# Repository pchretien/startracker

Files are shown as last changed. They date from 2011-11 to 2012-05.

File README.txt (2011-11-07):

Description

This is a merge of the two previous Stars Trackers I made. I wanted a model that could be both manual and motorized. This thing is "really" a work in progress since I have not taken any picture with it yet. In the next few days the moon will rise late so I'll give it a shot at the first clear sky.

This type of astrophotography mount is often called a barndoor mount, a scotch mount or a Haig mount. This mount allows you to take long exposure of the night sky by canceling out the apparent motion of the stars in the sky. 

You can get more information on this type of device on Wikipedia:
en.wikipedia.org/wiki/Barn_door_tracker.

The NEMA17 motor is driven by an Arduino arduino.cc and the Adafruit Motorshield adafruit.com. I am still working on the Arduino software. The objective is to compensate for the error induced by the linear motion trying to emulate a constant speed rotation.

I made a short video to demonstrate hot to change from the motorized version to the manual version of the Stars Tracker. 
youtube.com/watch?v=pLnhl2p-kOQ&feature=feedu

The drawings have been made using Sketchup. The original drawings can be found in the starstrackerv2.0.zip file.
Instructions

Print and assemble ... the important dimension is the distance between the center of the hinge and the pivots, which is 145mm.

The non-printed parts you will need:

Main assembly:
--------------
2x 3/8" threaded rod 6.25" long
8x 3/8" nuts
1x 3/8" bolt 3/4" long (camera head)
4x 608 bearings
1x M6x35 8mm shoulder bolt
3x M8 washers
1x M6 nut
1x 1/4" nut (tripod attachment)
1x 10mm diameter tube for polar alignment

Motor assembly:
---------------
4x M3x12 bolts
2x M3x8 bolts (coupling)
2x M3 nuts (coupling)
1x NEMA17 stepper motor
1x 1/4" 20TPI threaded rod 6" long
1x 10mm diameter and 20mm long cross-dowel with a threaded hole

Manual assembly:
----------------
5x 1/4" nuts
1x 1/4" butterfly nut
2x 3/16" #12 washers
1x 1/4" 20TPI threaded rod 6" long
1x 10mm diameter and 20mm long cross-dowel with a threaded hole

Electronic:
-----------
1x Arduino arduino.cc
1x Adafruit Motorshield adafruit.com/products/81

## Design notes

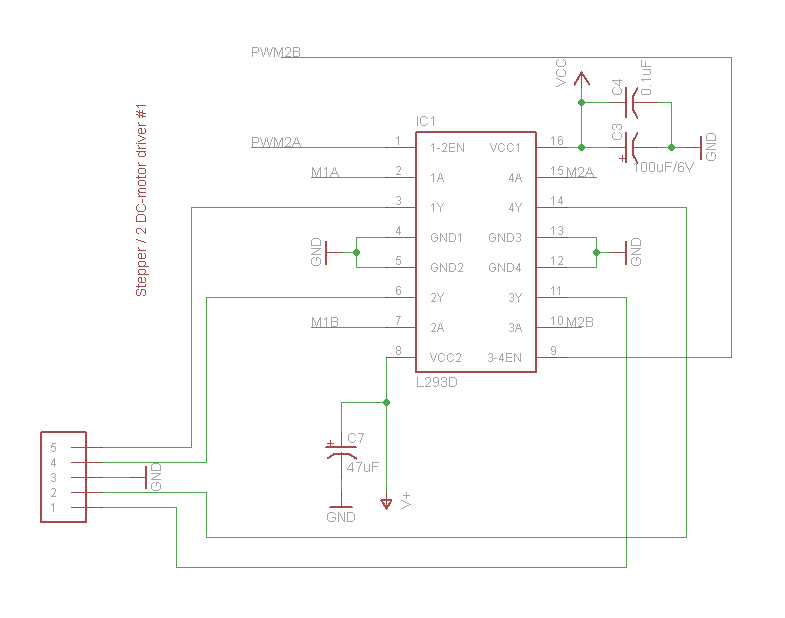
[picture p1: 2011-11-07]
L293Stepper.png

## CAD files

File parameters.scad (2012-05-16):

//
// Star tracker parameters
// Philippe Chrétien (2012)
// philippe.chretien.gmail.com
//

// Threaded rod
t_rod_out_radius = 4.8; //mm

// Skate bearing 608
bearing_out_radius = 11.25; //mm
bearing_thickness = 7.75; //mm

// M3 bolts
m3_out_radius = 1.5; //mm

// M3 nut
nut_m3_radius = 3.5; //mm
nut_m3_thickness = 2.5; //mm

// 1/4 nut
nut_1_4_radius = 6.5; //mm
nut_1_4_thickness = 5.5; //mm

// 3/8 nut
bolt_3_8_head_radius = 8.5; //mm
bolt_3_8_head_thickness = 6.0; //mm

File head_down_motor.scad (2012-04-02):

include <parameters.scad>

hdm_base_x = 43.0;
hdm_base_y = 53.0;
hdm_base_z = 15.4;
hdm_curve_radius = 40;

hdm_base_in_x = 30;
hdm_base_in_y = 33;

hdm_side_holes_y = 7.7;
hdm_side_holes_radius = 4.1;

hdm_buffer = 0.01;

module head_down_motor()
{
difference()
{
	// Piece stock
	union()
	{
		intersection()
		{
			translate([-1*(hdm_base_x/2),0,0])
				cube([hdm_base_x,hdm_base_y,hdm_base_z]);

			translate([0,hdm_base_y-hdm_curve_radius,0])
				cylinder(r=hdm_curve_radius, h=hdm_base_z, $fn=18);
		}			

		translate([-1*(hdm_base_x/2),0,0])
			cube([hdm_base_x,top_width,top_height]);		
	}	

	translate([-1*(hdm_base_in_x/2),0,0])
		cube([hdm_base_in_x,hdm_base_in_y,hdm_base_z]);

	translate([0,hdm_base_y, hdm_base_z/2])
		rotate(a=90, v=[1,0,0])
			cylinder(r=t_rod_out_radius, h=hdm_base_y-hdm_buffer);

	translate([-1*(hdm_base_x/2)-hdm_buffer,hdm_side_holes_y, hdm_base_z/2])
		rotate(a=90, v=[0,1,0])
			cylinder(r=t_rod_out_radius, h=hdm_base_x+2*hdm_buffer);
}
}

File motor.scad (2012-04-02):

include <parameters.scad>

base_x = 42.0;
base_y = 25.0;
base_z = 5.5;
curve_radius = 30;

top_width = 6.25;
top_height = 20;

screw_x = 15.5;		// Relative to the motor head hole center
screw_z = 15.5;		// Relative to the motor head hole center
screw_radius = 1.75;
screw_head_radius = 3.25;
screw_head_depth = 2.5;

pin_y = 3;
pin_height = 3;
pin_radius = 4.5; // Increased size but not yet printed

motor_head_z = 26.5;
motor_head_radius = 11.5;

buffer = 0.01;

module motor_half_mount()
{
	difference()
	{
		// Piece stock
		union()
		{
			intersection()
			{
				translate([-1*(base_x/2),0,0])
					cube([base_x,base_y,base_z]);

				translate([0,base_y-curve_radius,0])
					cylinder(r=curve_radius, h=base_z);
			}			

			translate([-1*(base_x/2),0,0])
				cube([base_x,top_width,top_height]);

			translate([0,base_y-pin_y-pin_radius,base_z])
				cylinder(r=pin_radius, h=pin_height, $fn=36);
		}	

		// Motor head hole
		translate([0,top_width+buffer,motor_head_z])
			rotate(a=90, v=[1,0,0])
				cylinder(r=motor_head_radius, h=top_width+2*buffer, $fn=36);

		// Screw holes
		translate([screw_x,top_width+buffer,motor_head_z-screw_z])
			rotate(a=90, v=[1,0,0])
				cylinder(r=screw_radius, h=top_width+2*buffer, $fn=36);

		translate([-1*screw_x,top_width+buffer,motor_head_z-screw_z])
			rotate(a=90, v=[1,0,0])
				cylinder(r=screw_radius, h=top_width+2*buffer, $fn=36);

		// Screw head pockets
		translate([screw_x,top_width+buffer,motor_head_z-screw_z])
			rotate(a=90, v=[1,0,0])
				cylinder(r=screw_head_radius, h=screw_head_depth, $fn=36);

		translate([-1*screw_x,top_width+buffer,motor_head_z-screw_z])
			rotate(a=90, v=[1,0,0])
				cylinder(r=screw_head_radius, h=screw_head_depth, $fn=36);
	}
}

module motor()
{
	translate([0,3,0])
		motor_half_mount();

	translate([0,-3,0])
		rotate(a=180, v=[0,0,1])
			motor_half_mount();
}

//motor();

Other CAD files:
wheel.scad
coupling.scad
head_down.scad
hinge6.scad
hinge7.scad
pivot.scad
plate1.scad
plate2.scad
tests.scad

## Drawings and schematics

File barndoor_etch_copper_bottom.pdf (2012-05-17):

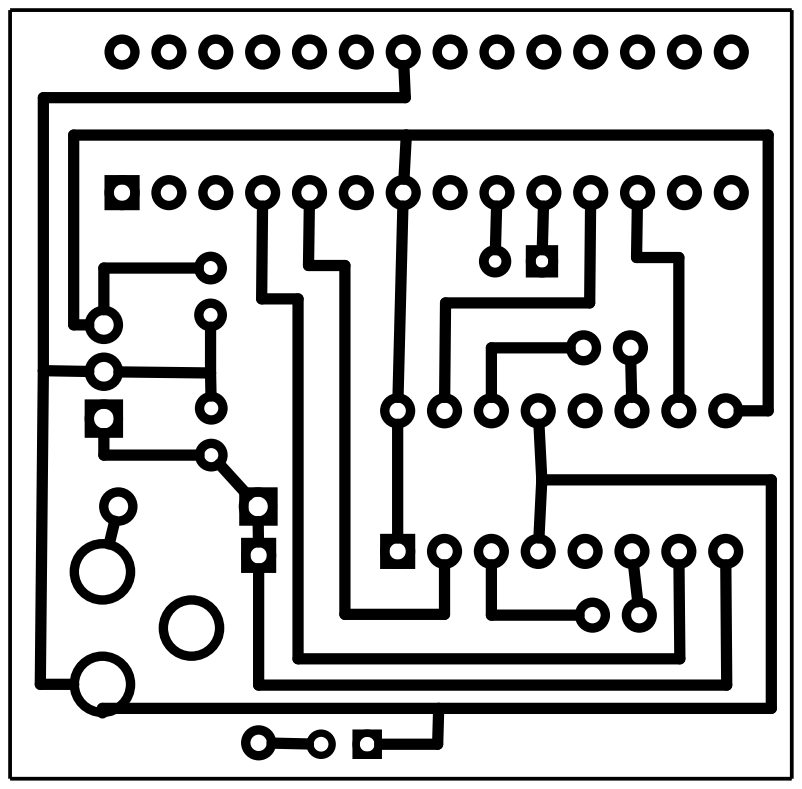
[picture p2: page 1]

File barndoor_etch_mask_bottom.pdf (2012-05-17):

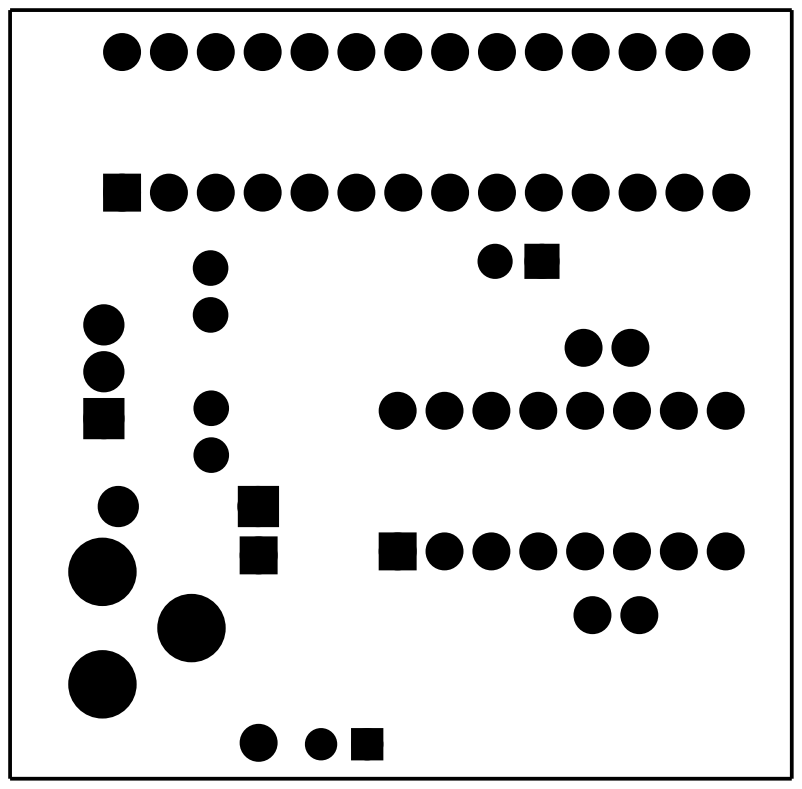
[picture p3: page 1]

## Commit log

2012-02-25 Started an OpenScad version
    [coupling.skp, coupling.stl, hinge6.scad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]
2012-02-27 Added hinge7.scad
    [hinge6.stl, hinge7.scad, hinge7.stl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]
2012-02-28 Added the motor mount and both forks
    [head_down.scad, head_down_motor.scad, motor.scad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]
2012-04-01 added coupling.scad and removed all stl files
    [ballj.stl, coupling.scad, coupling.stl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]
2012-04-01 Added pivot and wheel scads.
    [pivot.scad, wheel.scad, wheel2.skp]
2012-04-01 Removed skp files
    [ballj.scad, coupling.skp, crosshair.skp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]
2012-04-02 Added two plates for production
    [coupling.scad, head_down.scad, head_down_motor.scad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]
2012-05-16 Added M3 nut parameter
    [parameters.scad]
2012-05-16 Added the circuit schematics
    [barndoor.fzz]
2012-05-16 Added 0.1 micro F and a LED. The PCB is now 42x42mm
    [barndoor.fzz]
2012-05-17 Version of the first prototype
    [barndoor.fzz]
2012-05-23 Added jumpers to the Arduino pins
    [barndoor.fzz]
